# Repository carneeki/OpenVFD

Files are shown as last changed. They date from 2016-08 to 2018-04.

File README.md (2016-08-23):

# OpenVFD
Variable Frequency Drive for ATmega328 based Arduinos

A variable frequency drive is a method for controlling AC motors, typically used
in machinery such as a drill press, milling machine or lathe. A VFD typically
permits the use of running 3 phase motors on single phase power, and running
single phase motors on 3 phase power.

The Arduino code presented here will produce 3 PWM signals that approximate sine
waves suitable to drive some transistors that can be used to power AC motors.

EAGLE schematics will later pop up with potential (but untested) circuits that
can be used connect machinery.

VFDs follow several stages, and can be broken up into 3 separate circuits:

1. AC->DC rectification. This means that AC coming in is turned into DC power.
DC power is smoothed out for fewer ripples. This is where 3 phase really shines, there's a lot less ripple.
1. DC->AC inverter. Gnomes receive signals from a controller to turn a bunch of
switches on and off really fast so the motor thinks it sees AC power. Depending
on how fast the gnomes are clicking the switches controls how fast the motor
spins.
1. The controller is the final circuit, which the Arduino code concerns itself
with.

## AC->DC rectification
For single phase circuits, a standard bridge rectifier can be used.
For three phase circuits, a 3 phase rectifier is required (can be made from 6 diodes).

Once DC comes in, a smoothing capacitor (or a bank of them) is required. The
size of the caps depends on the power in and power out.

## DC->AC inverter
The gnomes mentioned are actually MOSFETs, a type of transistor. 6 of them are
hooked up with 3 in parallel from +DC to one leg of each motor. The other three
are connected from each leg of the motor to GND. The gate (or signal receiver)
needs to be hooked up correctly to the controller.

## Inverter Controller
This circuit consists of an Arduino producing three PWM sine waves that go
through a low pass filter. The low pass filter then goes into a device called a comparator. When the sine wave is high, one pin is turned on and goes to the
MOSFET connected to +DC and motor, the other pin is turned off which goes to
the MOSFET connected to the motor and GND.

Certain MOSFETs have trouble remaining on when high voltages are pushed through
them, so it may be necessary to use a controller chip that prevents certain
dangerous conditions, as well as providing an idea of how much juice the motor
is drawing.

## Thanks and references
Much of this code is very very similar to the works found at CPSU and AMAC
below, but with more comments, and designed for use in driving motors.

Omar David Munoz, senior project,
California Polytechnic State University
http://digitalcommons.calpoly.edu/cgi/viewcontent.cgi?article=1129&context=eesp

Martin Nawrath, "Arduino DDS Sine Wave Generator",
Academy of Media Arts Cologne
http://interface.khm.de/index.php/lab/interfaces-advanced/arduino-dds-sinewave-generator/

And the datasheet which is referenced quite a lot in OpenVFD.ino
http://www.atmel.com/images/Atmel-8271-8-bit-AVR-Microcontroller-ATmega48A-48PA-88A-88PA-168A-168PA-328-328P_datasheet_Complete.pdf

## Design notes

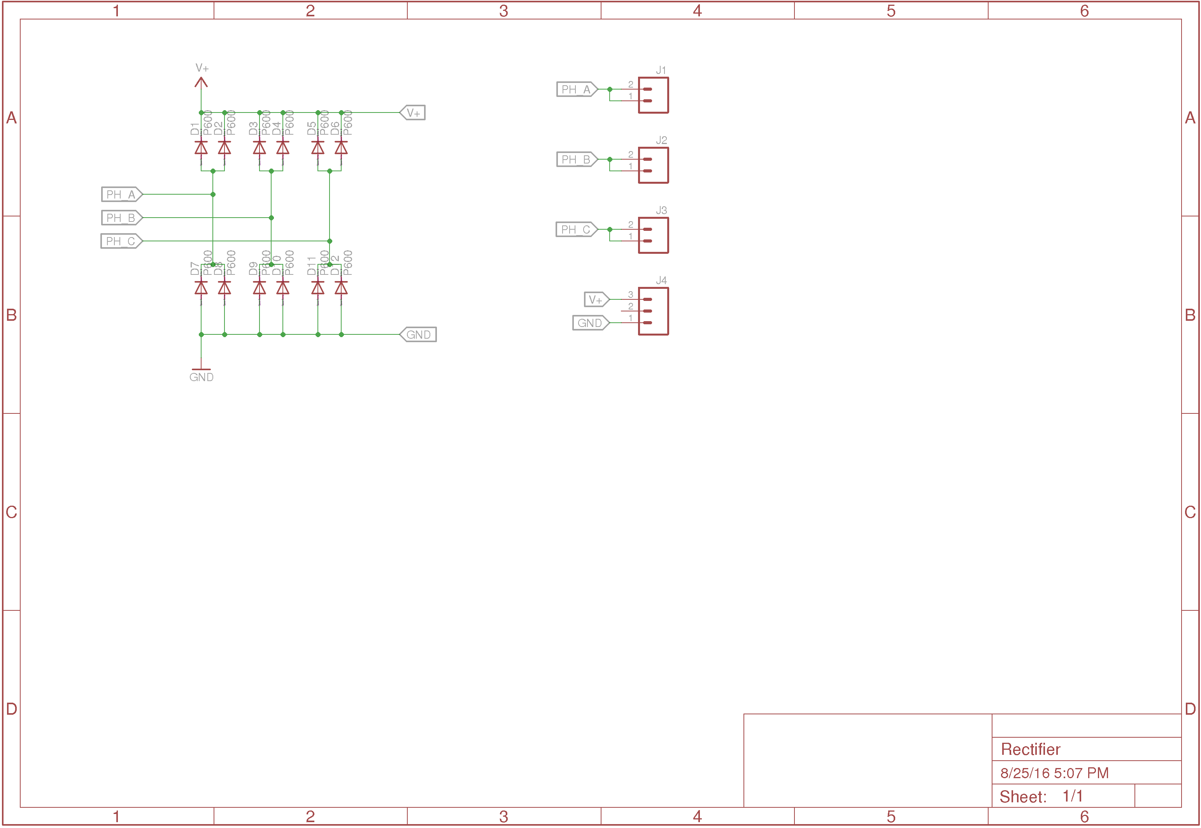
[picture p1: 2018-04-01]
cad/Rectifier Schematic.png

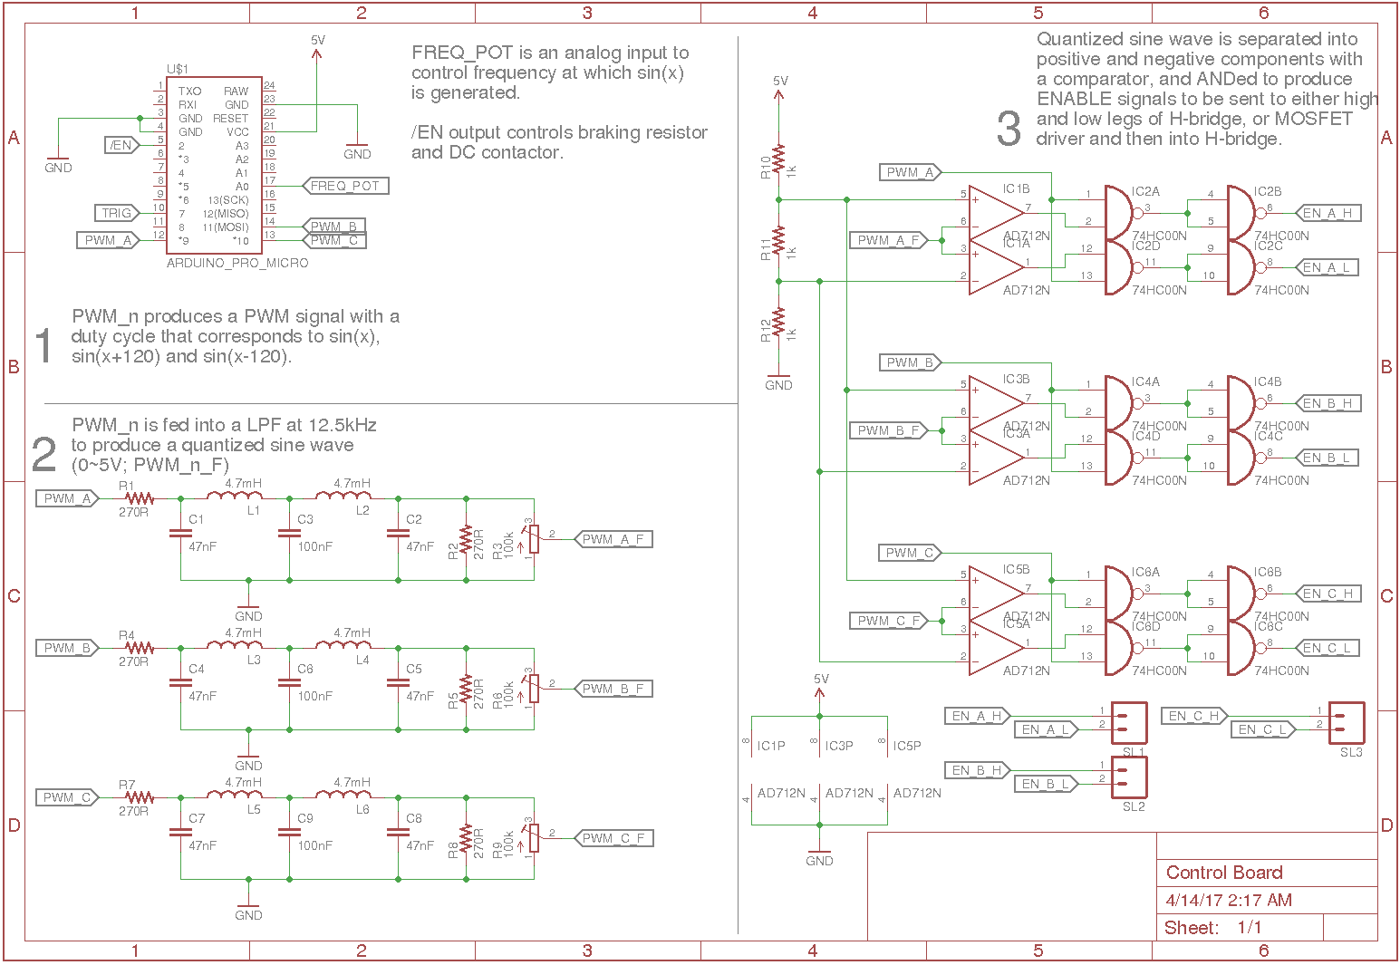
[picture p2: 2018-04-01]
cad/Control Schematic.png

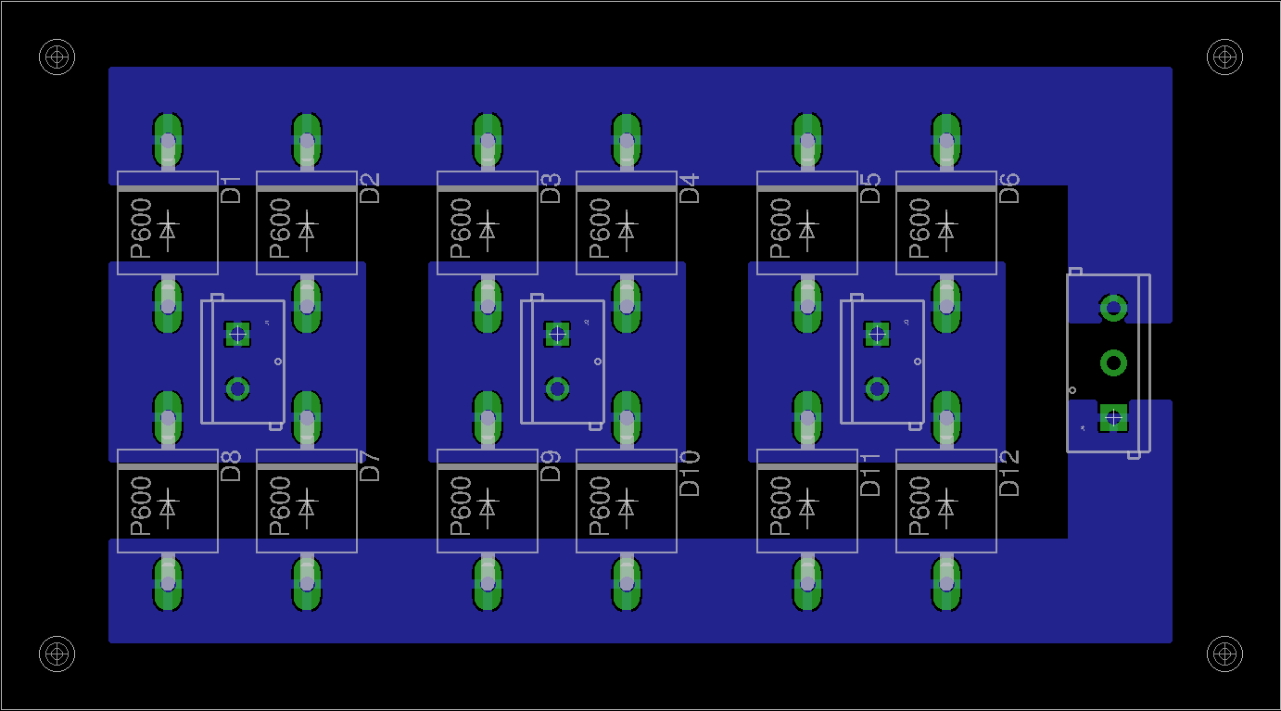
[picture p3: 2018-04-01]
cad/Rectifier Board.png

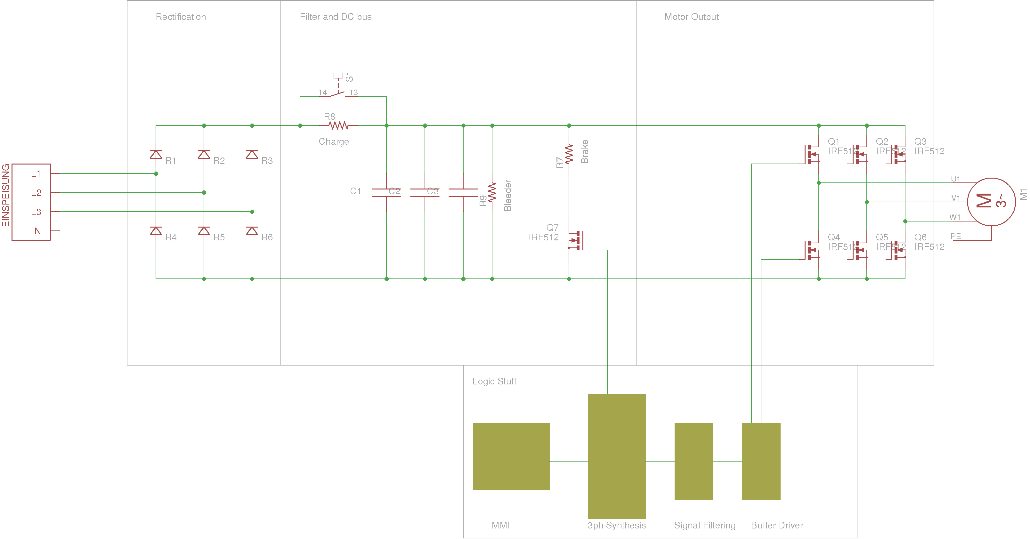
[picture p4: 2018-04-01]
cad/Block Diagram.png

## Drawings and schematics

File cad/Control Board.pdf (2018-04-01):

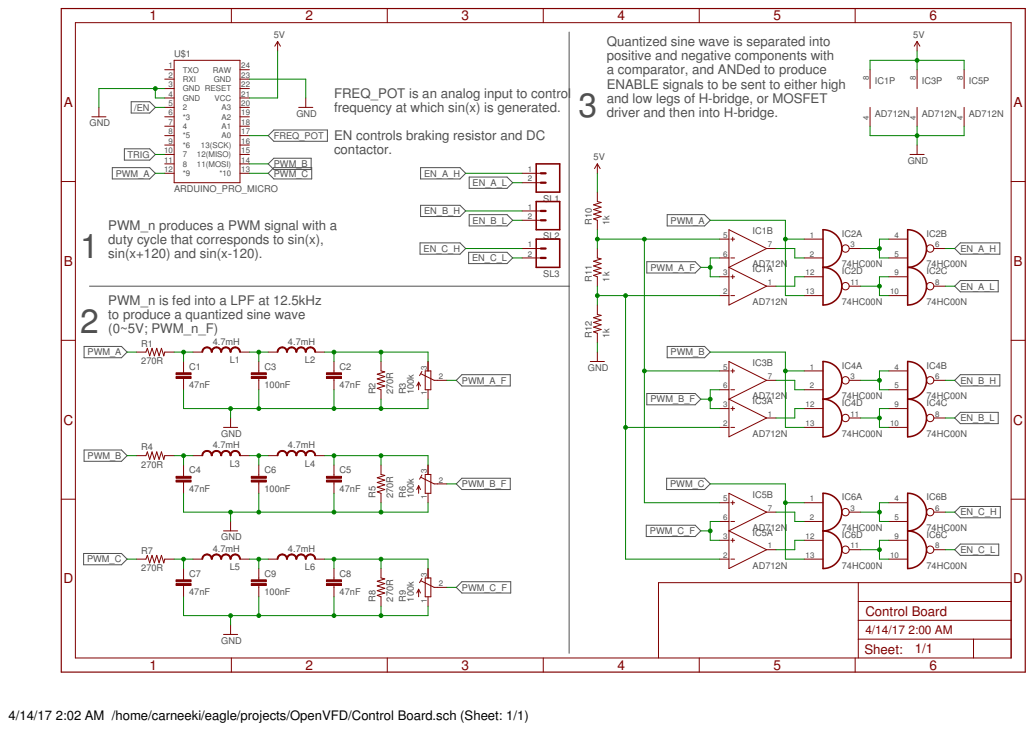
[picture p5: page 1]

Quantized sine wave is separated into
positive and negative components with
a comparator, and ANDed to produce
ENABLE signals to be sent to either high
and low legs of H-bridge, or MOSFET

FREQ_POT is an analog input to control
frequency at which sin(x) is generated. EN controls braking resistor and DC

driver and then into H-bridge. 1
GND

PWM_n produces a PWM signal with a
duty cycle that corresponds to sin(x), sin(x+120) and sin(x-120).
to produce a quantized sine wave
(0~5V; PWM_n_F)

PWM_n is fed into a LPF at 12.5kHz

4/14/17 2:02 AM /home/carneeki/eagle/projects/OpenVFD/Control Board.sch (Sheet: 1/1)

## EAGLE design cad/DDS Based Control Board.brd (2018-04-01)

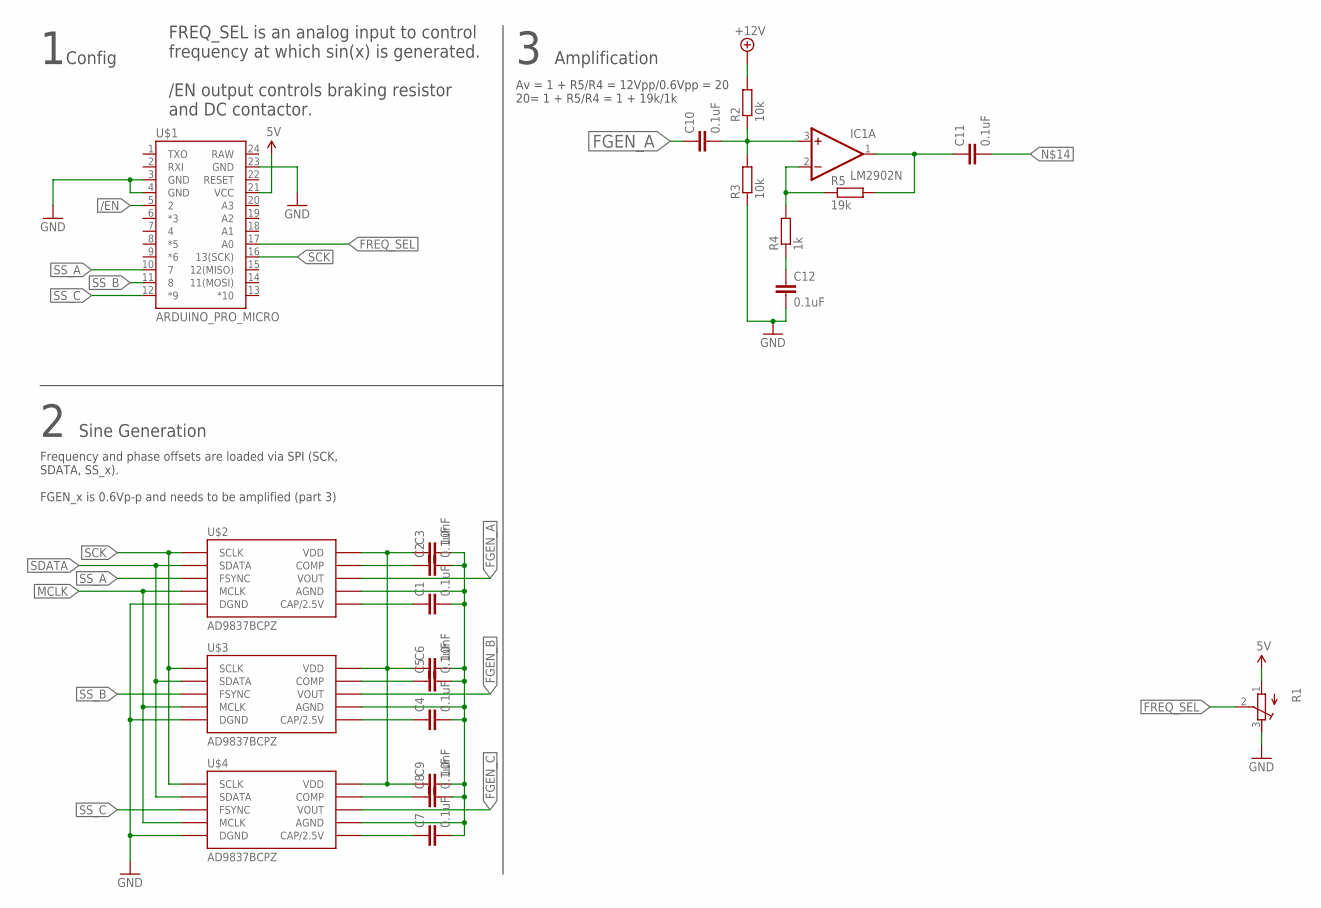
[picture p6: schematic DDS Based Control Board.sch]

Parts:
C1, C2, C4, C5, C7, C8, C10, C11, C12: 0.1uF; C025-025X050
C3, C6, C9: 10nF; C025-025X050
IC1: LM2902N; DIL14
R1: R-TRIMM64X; RTRIM64X
R2, R3: 10k; 0207/7
R4: 1k; 0207/7
R5: 19k; 0207/7
U$1: ARDUINO_PRO_MICRO
U$2, U$3, U$4: AD9837BCPZ; AD9837

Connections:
5V: R1.1 (A)
+12V: R2.2
/EN: U$1.5 (2)
FGEN_A: C10.1, U$2.P$10 (VOUT)
FGEN_B: U$3.P$10 (VOUT)
FGEN_C: U$4.P$10 (VOUT)
FREQ_SEL: R1.2 (S), U$1.17 (A0)
GND: C12.2, R1.3 (E), R3.1, U$1.3 (GND), U$1.4 (GND), U$1.23 (GND)
MCLK: U$2.P$5 (MCLK), U$3.P$5 (MCLK), U$4.P$5 (MCLK)
unnamed: C3.1, C6.1, C9.1, U$2.P$2 (VDD), U$3.P$2 (VDD), U$4.P$2 (VDD)
unnamed: C1.2, C2.2, C3.2, C4.2, C5.2, C6.2, C7.2, C8.2, C9.2, U$2.P$9 (AGND), U$3.P$9 (AGND), U$4.P$9 (AGND)
unnamed: C1.1, U$2.P$3 (CAP/2.5V)
unnamed: U$2.P$0 (DGND), U$2.P$4 (DGND), U$3.P$0 (DGND), U$3.P$4 (DGND), U$4.P$0 (DGND), U$4.P$4 (DGND)
unnamed: C2.1, U$2.P$1 (COMP)
unnamed: C5.1, U$3.P$1 (COMP)
unnamed: C8.1, U$4.P$1 (COMP)
unnamed: C7.1, U$4.P$3 (CAP/2.5V)
unnamed: C4.1, U$3.P$3 (CAP/2.5V)
unnamed: C10.2, IC1.3 (+IN), R2.1, R3.2
unnamed: C11.1, IC1.1 (OUT), R5.2
unnamed: IC1.2 (-IN), R4.2, R5.1
unnamed: C12.1, R4.1
SCK: U$1.16 (13(SCK)), U$2.P$7 (SCLK), U$3.P$7 (SCLK), U$4.P$7 (SCLK)
SDATA: U$2.P$6 (SDATA), U$3.P$6 (SDATA), U$4.P$6 (SDATA)
SS_A: U$1.10 (7), U$2.P$8 (FSYNC)
SS_B: U$1.11 (8), U$3.P$8 (FSYNC)
SS_C: U$1.12 (*9), U$4.P$8 (FSYNC)
V+: IC1.4 (V+)
V-: IC1.11 (V-)
VCC: U$1.21 (VCC)

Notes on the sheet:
FREQ_SEL is an analog input to control frequency at which sin(x) is generated. /EN output controls braking resistor and DC contactor.
Frequency and phase offsets are loaded via SPI (SCK, SDATA, SS_x). FGEN_x is 0.6Vp-p and needs to be amplified (part 3)
Config
Sine Generation
Amplification
Av = 1 + R5/R4 = 12Vpp/0.6Vpp = 20 20= 1 + R5/R4 = 1 + 19k/1k

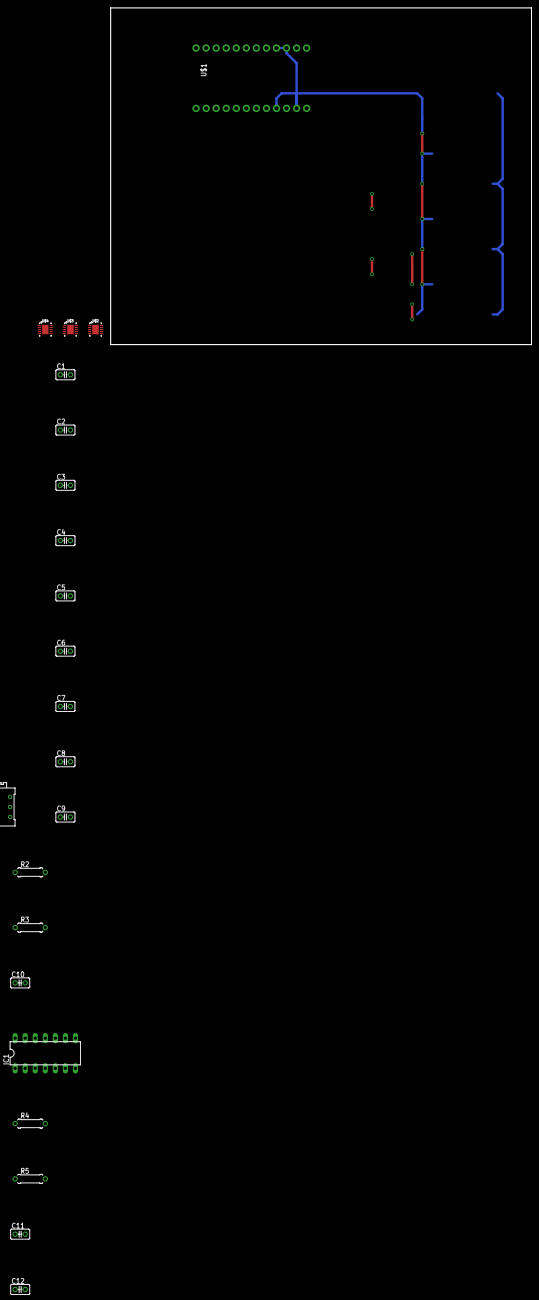
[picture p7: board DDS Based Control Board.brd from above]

Board: 2 copper layers, 106.3 x 85.1 mm, 22 parts (0 on the bottom side), 22 nets.

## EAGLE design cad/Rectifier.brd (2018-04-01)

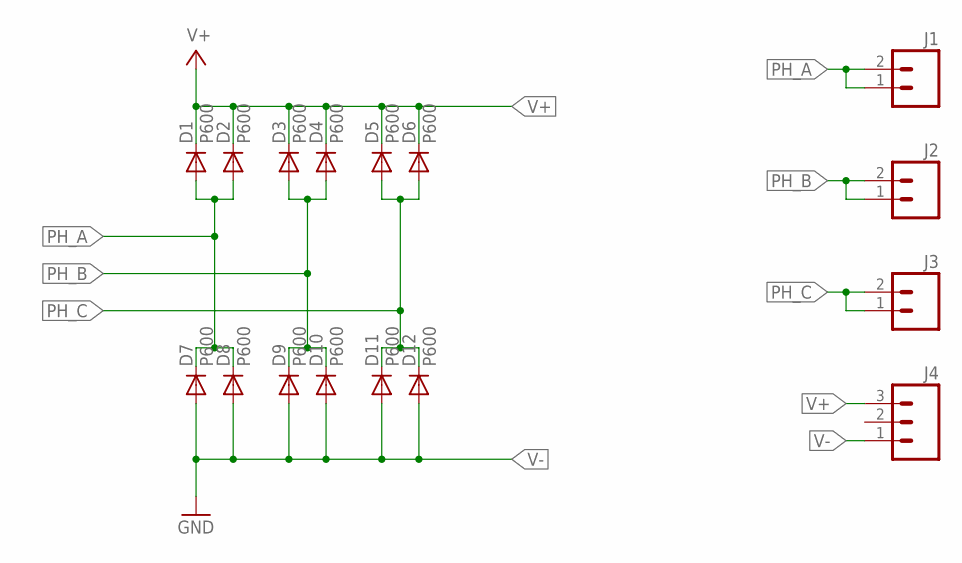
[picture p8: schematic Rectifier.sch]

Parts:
D1, D2, D3, D4, D5, D6, D7, D8, D9, D10, D11, D12: P600; P6-15
J1, J2, J3: M025MM; SCREWTERMINAL-5MM-2
J4: M03-SCREW-5MM; SCREWTERMINAL-5MM-3

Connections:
PH_A: D1.A, D2.A, D7.C, D8.C, J1.1, J1.2
PH_B: D3.A, D4.A, D9.C, D10.C, J2.1, J2.2
PH_C: D5.A, D6.A, D11.C, D12.C, J3.1, J3.2
V+: D1.C, D2.C, D3.C, D4.C, D5.C, D6.C, J4.3
V-: D7.A, D8.A, D9.A, D10.A, D11.A, D12.A, J4.1

Board: 2 copper layers, 16 parts (0 on the bottom side), 5 nets, no tracks yet.

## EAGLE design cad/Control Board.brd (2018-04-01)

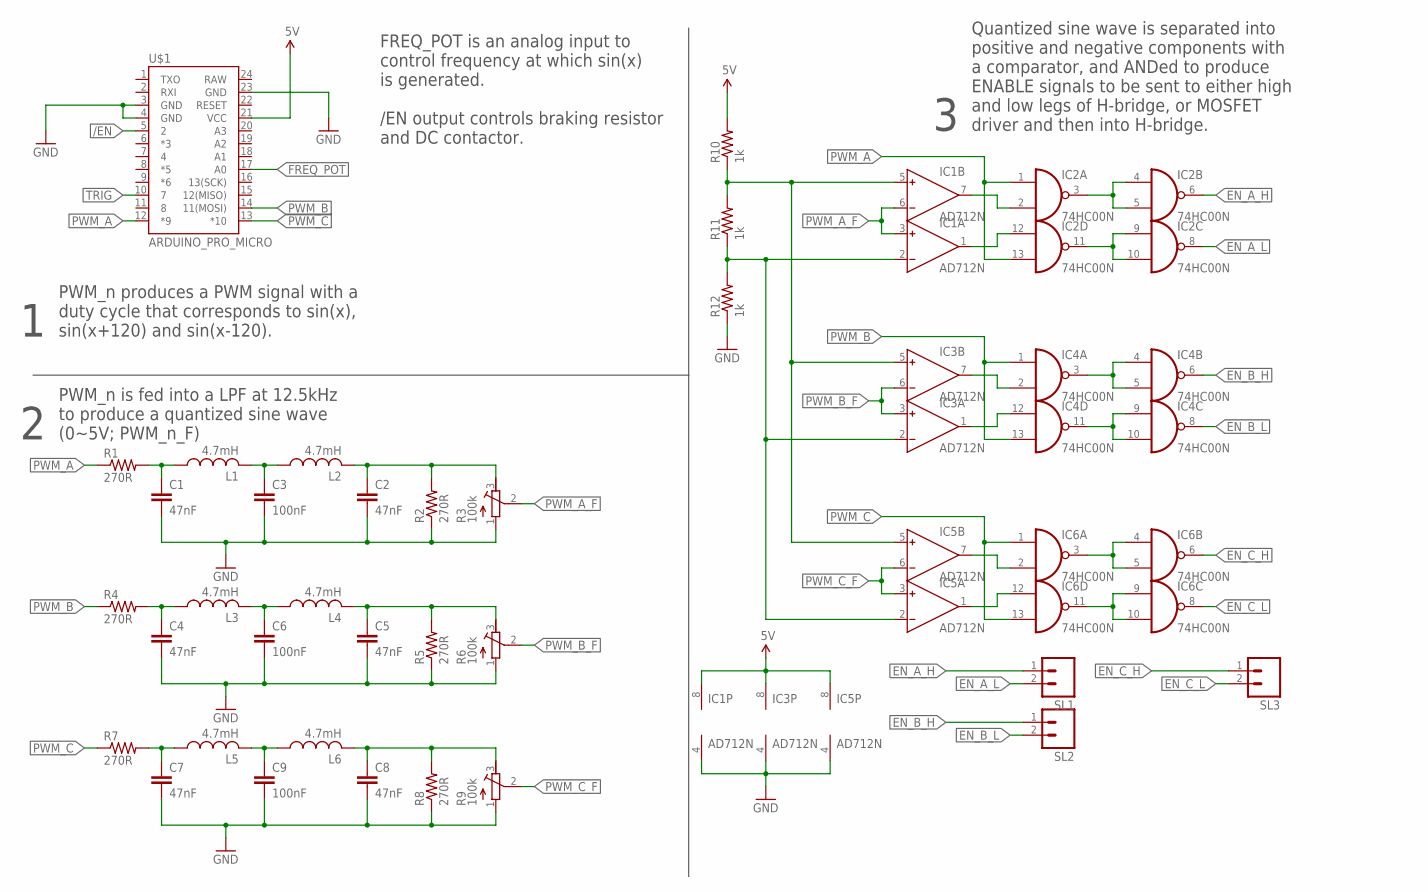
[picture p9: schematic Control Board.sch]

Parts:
C1, C2, C4, C5, C7, C8: 47nF; C025-025X050
C3, C6, C9: 100nF; C025-025X050
IC1, IC3, IC5: AD712N; DIL08
IC2, IC4, IC6: 74HC00N; DIL14
L1, L2, L3, L4, L5, L6: 4.7mH; 0207/12
R1, R2, R4, R5, R7, R8: 270R; 0207/7
R3, R6, R9: 100k; RTRIM3296W
R10, R11, R12: 1k; 0207/7
SL1, SL2, SL3: M02PTH; 1X02
U$1: ARDUINO_PRO_MICRO

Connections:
/EN: U$1.5 (2)
EN_A_H: IC2.6 (O), SL1.1
EN_A_L: IC2.8 (O), SL1.2
EN_B_H: IC4.6 (O), SL2.1
EN_B_L: IC4.8 (O), SL2.2
EN_C_H: IC6.6 (O), SL3.1
EN_C_L: IC6.8 (O), SL3.2
FREQ_POT: U$1.17 (A0)
GND: C1.2, C2.2, C3.2, C4.2, C5.2, C6.2, C7.2, C8.2, C9.2, IC1.4 (V-), IC2.7 (GND), IC3.4 (V-), IC4.7 (GND), IC5.4 (V-), IC6.7 (GND), R2.1, R3.1 (A), R5.1, R6.1 (A), R8.1, R9.1 (A), R12.1, U$1.3 (GND), U$1.4 (GND), U$1.23 (GND)
unnamed: C1.1, L1.1, R1.2
unnamed: C3.1, L1.2, L2.1
unnamed: C2.1, L2.2, R2.2, R3.3 (E)
unnamed: C4.1, L3.1, R4.2
unnamed: C6.1, L3.2, L4.1
unnamed: C5.1, L4.2, R5.2, R6.3 (E)
unnamed: C7.1, L5.1, R7.2
unnamed: C9.1, L5.2, L6.1
unnamed: C8.1, L6.2, R8.2, R9.3 (E)
unnamed: IC1.7 (OUT), IC2.2 (I1)
unnamed: IC1.1 (OUT), IC2.12 (I0)
unnamed: IC3.7 (OUT), IC4.2 (I1)
unnamed: IC1.5 (IN+), IC3.5 (IN+), IC5.5 (IN+), R10.1, R11.2
unnamed: IC1.2 (IN-), IC3.2 (IN-), IC5.2 (IN-), R11.1, R12.2
unnamed: IC3.1 (OUT), IC4.12 (I0)
unnamed: IC5.7 (OUT), IC6.2 (I1)
unnamed: IC5.1 (OUT), IC6.12 (I0)
unnamed: IC2.3 (O), IC2.4 (I0), IC2.5 (I1)
unnamed: IC2.9 (I0), IC2.10 (I1), IC2.11 (O)
unnamed: IC4.3 (O), IC4.4 (I0), IC4.5 (I1)
unnamed: IC4.9 (I0), IC4.10 (I1), IC4.11 (O)
unnamed: IC6.9 (I0), IC6.10 (I1), IC6.11 (O)
unnamed: IC6.3 (O), IC6.4 (I0), IC6.5 (I1)
PWM_A: IC2.1 (I0), IC2.13 (I1), R1.1, U$1.12 (*9)
PWM_A_F: IC1.3 (IN+), IC1.6 (IN-), R3.2 (S)
PWM_B: IC4.1 (I0), IC4.13 (I1), R4.1, U$1.14 (11(MOSI))
PWM_B_F: IC3.3 (IN+), IC3.6 (IN-), R6.2 (S)
PWM_C: IC6.1 (I0), IC6.13 (I1), R7.1, U$1.13 (*10)
PWM_C_F: IC5.3 (IN+), IC5.6 (IN-), R9.2 (S)
TRIG: U$1.10 (7)
VCC: IC1.8 (V+), IC2.14 (VCC), IC3.8 (V+), IC4.14 (VCC), IC5.8 (V+), IC6.14 (VCC), R10.2, U$1.21 (VCC)

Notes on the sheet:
FREQ_POT is an analog input to control frequency at which sin(x) is generated. /EN output controls braking resistor and DC contactor.
PWM_n is fed into a LPF at 12.5kHz to produce a quantized sine wave (0~5V; PWM_n_F)
Quantized sine wave is separated into positive and negative components with a comparator, and ANDed to produce ENABLE signals to be sent to either high and low legs of H-bridge, or MOSFET driver and then into H-bridge.
PWM_n produces a PWM signal with a duty cycle that corresponds to sin(x), sin(x+120) and sin(x-120).

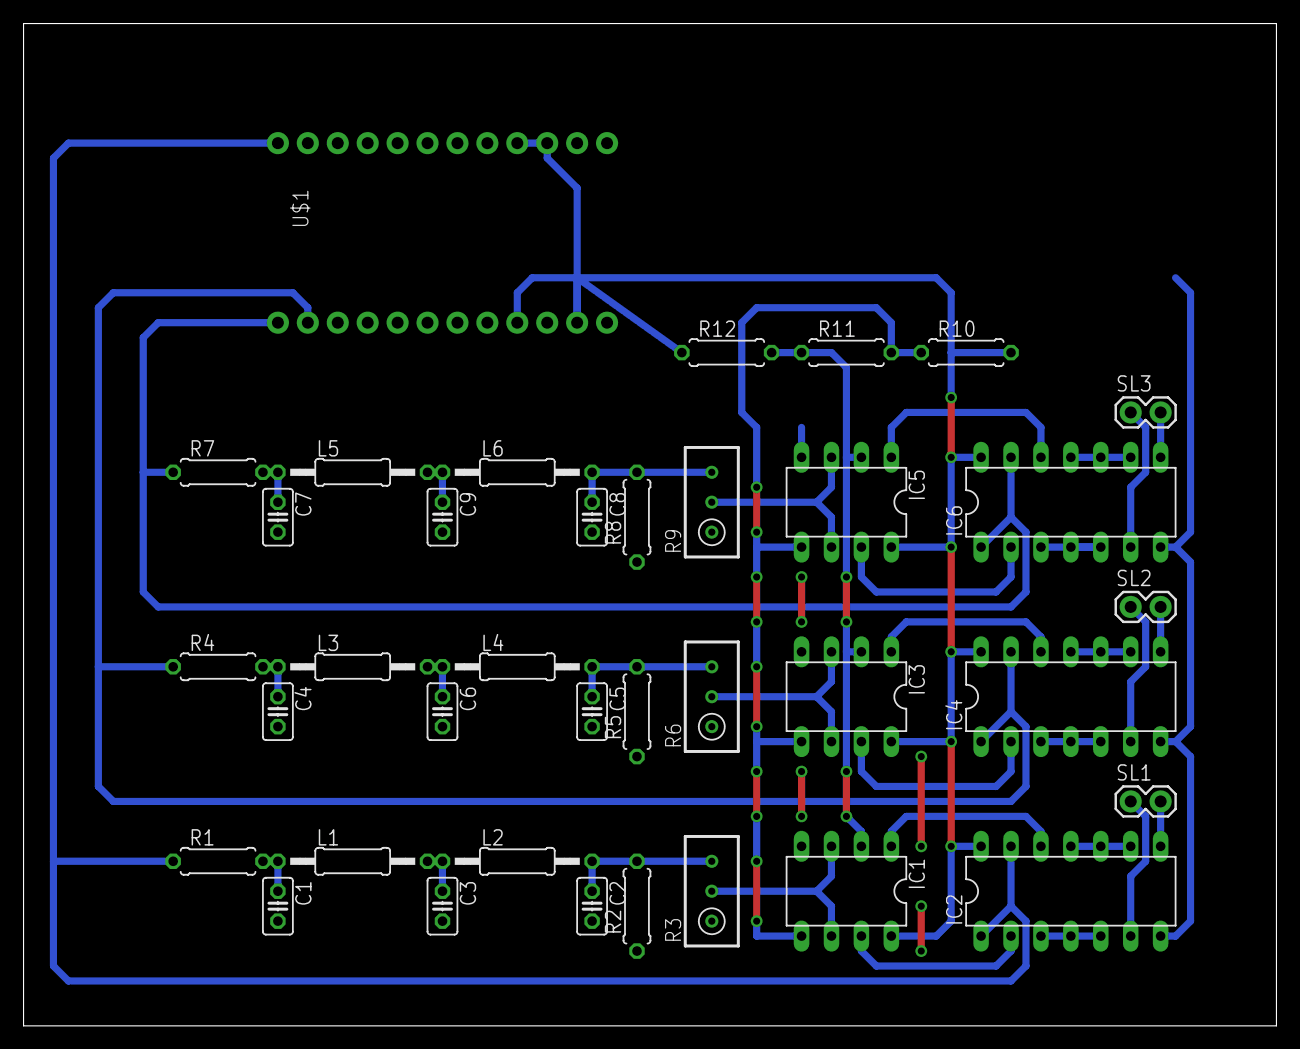
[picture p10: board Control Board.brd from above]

Board: 2 copper layers, 106.3 x 85.1 mm, 37 parts (0 on the bottom side), 37 nets.

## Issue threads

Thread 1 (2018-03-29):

can you share a working circuit for VFD along with arduino?

amrithmmh, 2018-03-29:
i am really interested in your project thanks

carneeki, 2018-04-01:
This project had to take a bit of a back seat for a while, but I want to get back on it soon!

I've just pushed some cad files I was working on a while ago, I'm not sure if they will work, but feel free to review them. If nothing else, the block diagram might be a good place to start a new VFD project.

amrithmmh, 2018-04-25:
you might be interested in this
http://www.microchip.com//wwwAppNotes/AppNotes.aspx?appnote=en567897
http://ww1.microchip.com/downloads/en/AppNotes/00001660B.pdf
file:///C:/Users/Novatek/AppData/Local/Temp/BNZ.5ae0150e714456/219-0503c_SCH.pdf

carneeki, 2018-04-25:
These application notes are great thanks! It makes me the idea in my head might be on the right track.

As for knowledge or experience, that hasn't stopped me in the past! My strategy is to set myself some projects and work out what I need to learn, and then learn it. With mixed results ;)

carneeki, 2018-04-25:
As I don't know what your experience is... I should mention a word of caution though: VFDs typically operate at voltages that can be lethal. If you're new to electronics, I would recommend starting off with some low voltage projects (anything between 0 and 12V should be fine) to build up your skills, and use bought power supplies that have passed the important safety checks.

amrithmmh, 2018-04-25:
there are many ICs from microchip too that have application notes you can check out those too
and one more IC
https://www.nxp.com/docs/en/data-sheet/MC3PHAC.pdf
http://application-notes.digchip.com/314/314-67275.pdf
http://sroogle.ru/?q=MC3PHAC
http://www.electronics-lab.com/project/3-phase-ac-motor-controller/
MC3PHAC is retired though :(

carneeki, 2018-04-25:
True, I've got a couple of PIC chips in a drawer somewhere, however, I'm thinking something like the Arduino Nano will have less of a steep learning curve to people like CNC machinists who may be wanting to build a VFD. Plug USB cable in and push the 'Upload' button.

If something like a USBasp or PICkit are needed for ICSP, that adds an additional barrier to entry. If I were making a commercial product, I'd look at going either PIC or AVR without the Arduino framework, but keeping it accessible for the mechatronics enthusiast is important.

dexterbot80, 2019-02-07:
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
Hello, Here is an update for testing PCB . I hope it will work :)

dexterbot80, 2019-02-07:
What are the TRIG and / EN pins? Thank you

carneeki, 2019-02-08:
Hi @dexterbot80  the board looks great!

TRIG is to trigger an oscilloscope (during testing / calibration) - see line `19` in `OpenVFD.ino` ;)
/EN I think was to be an "Enable" pin where pulling it low would enable the PWM outputs and pulling it high would disable the outputs, this is because controllers like Grbl often use a "Spindle Enable" output pin to tell the VFD to start the spindle, but it could also be used for a manual switch. A simple `if()` inside of `loop()` should be all that's needed to make it functional.

dexterbot80, 2019-02-08:
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
Thank you

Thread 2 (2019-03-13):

Inappropriate transistors

Harvie, 2019-03-13:
Hi! according to Block Diagram.png you are using IRF512 transistors, but i've checked datasheet and these came in 100V maximum rating. I guess that commercial VFDs use IGBT transistors... Don't know.

But you surely get more  than 100V when rectifiing mains AC, no matter if US 120V or EU 230V...
Also 230V is RMS, while after rectification you get peak value 320V rather than the RMS. (multiply by factor of 1.41421)
But if you are rectifiing 3 phases, that's different story. There is 400V RMS between two phases, which means peak is something like 566V, so that's what you get after rectifiing 3F mains in EU. (multiply by 1.5708)

So to know what voltage you THEORETICALY get after rectification of 3 phases:

**EU: 230*1.5708*1.41421 = 511V
US: 120*1.5708*1.41421 = 267V**

Note that the voltage in grid fluctuates a little. Also you should leave some safety margin.

Please keep that in mind.

carneeki, 2019-03-14:
@Harvie absolutely correct on the count of voltage, nice find. :)

IIRC, the block diagram was the very first diagram I did to get a "big picture" overview - the idea being that each area of the diagram would have separate schematics with values, and I likely forgot to remove the component values from the block diagram.

I seem to remember another IRF branded IGBT in the output schematic with a voltage rating of 600V, and thinking that 90V for AU (also 230V, +8%/-10%) wasn't a lot of margin [in theory could be about 680V for our power here]... However, there are two IGBTs in series (as well as the motor) along each path from +ve to GND along the DC bus, so it works out to about 300V across the drain and source on each IGBT.

Out of curiosity, where does 1.5708 come from? I recognise 1.414... = sqrt(2), and 1.732... = sqrt(3) which were both common constants in 3ph power calculations, but 1.5708... is a new one to me.

Thanks again for spotting this :)

Harvie, 2019-03-14:
> Out of curiosity, where does 1.5708 come from?

I am not really sure, since i've never designed 3 phase appliance. I've just googled the number and 1.57 seems to repeat through te internet. However i draw these two green arrows to the following diagram. I seems to be more like 1.5 or 1.49 in picture, i don't know why everybody uses 1.57. Maybe i am missing something. But i guess there's more to it:

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

> However, there are two IGBTs in series (as well as the motor) along each path from +ve to GND along the DC bus

I don't think so:

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

If you want possitive voltage on U1, you have to open Q1 and close Q4. That would mean that Q4 gets full DC rail voltage.

Also you can't assume anything about the motor. VFDs should be able to work with low-impedance low-voltage motors for several reasons.

1.) when you lower the RPM, you lower the frequency and the impedance goes very low. That's why common VFDs for CNC spindles have to dramaticaly lower the sine voltage at the low RPMs. That's why all VFDs have programmable voltage/frequency curves.

2.) you might want VFD to drive small motor that can't handle 230V at all. For example you might want to drive small BLDC motor using VFD.

3.) VFD should have closed-loop current sensing. I've accidentaly managed to get some metalic chips to the connector of my CNC spindle and that effectively created short circuit of VFD. I should have been more carefull, but to be honest the metalic shavings are very common around CNC.
I am very happy that VFD managed to detect the short circuit, stop itself and display appropriate error message instead of exploding transistors...

carneeki, 2019-03-14:
> But i guess there's more to it:
Perhaps this image will help?
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

It's from the section of [Full-wave Three-phase Rectifier Conduction Waveform](https://www.electronics-tutorials.ws/power/three-phase-rectification.html) here which offers an explanation of a slightly higher than 1.57x constant (approx 1.65) is needed. Overlayed with a variation on your image I think it makes sense:
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

I took your P2 to P1 voltage and copy+pasted it next to the yellow line I drew and the yellow line is longer just a little bit either side of the valley - the gradient of P3 is near zero so the rate of change is also near zero, but the gradient of P2 is closer to 1 so the rate of change is more. (btw, I honestly never thought I'd use calculus in a discussion on the internet :D !)

> If you want possitive voltage on U1, you have to open Q1 and close Q4. That would mean that Q4 gets full DC rail voltage.
Yep - this is true... It makes more sense now that I see the H-bridge on paper again, and to pretend the IGBTs are switches.

Concerning:
1. Lower voltage - I think they simply use PWM to do this in software no? Would be interesting to put an oscilloscope on the output terminals of the FETs to take a look. If so, this become a matter of software chopping the open/close ratios.
2. Low voltage DC would also be a matter of software chopping PWM, but maybe with additional timing constraints - I've never looked at BLDC control before.
3. The output schematic includes an IRS2336, the [datasheet](https://www.infineon.com/dgdl/Infineon-IRS2336-DS-v02_00-EN.pdf?fileId=5546d462533600a40153567ab2a0280e) indicates it has short and shoot-thru protections, as well as fault reporting. It requires hooking up the Itrip pin to some shunt resistors. I'll add that to the growing TODO list :)

Harvie, 2019-03-14:
> I think they simply use PWM to do this in software no?

Of course. But that was not my point. My point is that in such case you have to drop all DC rail voltage on the transistor, so you can't count with motor to drop any aditional voltage to save your transistors.

> Low voltage DC would also be a matter of software chopping PWM.  I've never looked at BLDC control before.

BLDC is exactly the same as 3 phase AC motor. The **DC** in BLDC stands just for the fact that they use "speed controller" to run on DC. Speed controller is basicaly just VFD without rectifier on input. BLDC terminology is used by RC model people (drones, rc airplanes, e-bikes, etc...), so that means BLDC motor usualy runs much lower voltages, because they use batteries to power them. Technicaly speaking it's exactly the same as AC motor. The BLDC term is bit misleading... But if you think about it... Even brushed DC motors run on AC. They just have to create it using brushes.

> The output schematic includes an IRS2336, the datasheet indicates it has short and shoot-thru protections, as well as fault reporting.

This is very cool! At least if that's really true... Is it really protecting short through the IGBTs? Or it's just protecting the driver output from being shorted?

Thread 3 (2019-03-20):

Your proposed circuit is wrong,

dexterbot80, 2019-03-20:
The AD712 comparator requires differential input voltage. https://www.analog.com/media/en/technical-documentation/data-sheets/ad712.pdf
I replaced with LM358N but the IGBT bridge goes into short circuit immediately after the start.
http://www.ti.com/lit/ds/symlink/lm158-n.pdf

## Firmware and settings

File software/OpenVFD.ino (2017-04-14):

#include "avr/pgmspace.h" // PROGMEM and pgm_read_byte_near()
#include "avr/io.h"

/* Reference clock needs to be measured for the crystal per board (about 16MHz).
 * It is then divided by 510.
 * 16M / 510 = 31372.5490
 */
#define REFCLK 31372.549 // TODO: measure me and adjust

// output frequency
#define FREQ_POT A0  // analog input (A0..A4 are valid) default: A0
#define FREQ_MIN 0   // default: 0
#define FREQ_MAX 100 // default: 100

// pot values might not permit cranking full range so adjust here
#define POT_MIN 0    // default: 0
#define POT_MAX 1023 // default: 1023

// pins for 3 phases: Alpha, Bravo, Charlie, and trigger for CRO.
// ATMega 168 / 328 valid PWM pins are 3,5,6,9,10,11. Non-default values have
// not been tested
#define PWM_A  9     // default:  9
#define PWM_B 10     // default: 10
#define PWM_C 11     // default: 11
#define TRIG   7     // default:  7

/*******************************************************************************
 * Should not need to configure anything below here ***************************/

/*
 * LUT for sin(t) generated (by spreadsheet) using this formula:
 * x = ROUND( (255/2) * (1+SIN((2*PI()) * (t/256))) )
 *
 * where 0 <= t <= 255 ; keeping one period of sine in nvram
 *
 * Keeping LUT is way faster than calculating all the time
 */
const byte sin256[] PROGMEM =
{
//  0   1   2   3   4   5   6   7   8   9   a   b   c   d   e   f
  128,131,134,137,140,143,146,149,152,155,158,162,165,167,170,173, // 00:0f
  176,179,182,185,188,190,193,196,198,201,203,206,208,211,213,215, // 10:1f
  218,220,222,224,226,228,230,232,234,235,237,238,240,241,243,244, // 20:2f
  245,246,248,249,250,250,251,252,253,253,254,254,254,255,255,255, // 30:3f
  255,255,255,255,254,254,254,253,253,252,251,250,250,249,248,246, // 40:4f
  245,244,243,241,240,238,237,235,234,232,230,228,226,224,222,220, // 50:5f
  218,215,213,211,208,206,203,201,198,196,193,190,188,185,182,179, // 60:6f
  176,173,170,167,165,162,158,155,152,149,146,143,140,137,134,131, // 70:7f
  128,124,121,118,115,112,109,106,103,100, 97, 93, 90, 88, 85, 82, // 80:8f
   79, 76, 73, 70, 67, 65, 62, 59, 57, 54, 52, 49, 47, 44, 42, 40, // 90:9f
   37, 35, 33, 31, 29, 27, 25, 23, 21, 20, 18, 17, 15, 14, 12, 11, // a0:af
   10,  9,  7,  6,  5,  5,  4,  3,  2,  2,  1,  1,  1,  0,  0,  0, // b0:bf
    0,  0,  0,  0,  1,  1,  1,  2,  2,  3,  4,  5,  5,  6,  7,  9, // c0:cf
   10, 11, 12, 14, 15, 17, 18, 20, 21, 23, 25, 27, 29, 31, 33, 35, // d0:df
   37, 40, 42, 44, 47, 49, 52, 54, 57, 59, 62, 65, 67, 70, 73, 76, // e0:ef
   79, 82, 85, 88, 90, 93, 97,100,103,106,109,112,115,118,121,124  // f0:ff
};

// phase offsets (n * 255 / 3)
#define A_OFFSET 0   // (0x00)
#define B_OFFSET 85  // (0x55)
#define C_OFFSET 170 // (0xaa)

int freq; // output frequency
const double TUN_K=( 4294967296.0 / REFCLK ); // tuning coefficient

// variables in ISR
volatile byte icnt;            //
volatile byte icnt1;           //
volatile byte c4ms;            // counter incremented every 4ms
volatile unsigned long phaccu; // phase accumulator
volatile unsigned long tune;   // dds tuning word

void setup()
{
  pinMode(PWM_A, OUTPUT);
  pinMode(PWM_B, OUTPUT);
  pinMode(PWM_C, OUTPUT);
  pinMode(TRIG, OUTPUT);

  setup_timers(); // this also disables interrupts
}

void loop()
{
  if(c4ms > 250)
  {
    c4ms = 0;
    freq = map(analogRead(FREQ_POT), POT_MIN, POT_MAX, FREQ_MIN, FREQ_MAX);

    TIMSK2 &= ~(_BV(TOIE2)); // disable Timer2 interrupt
    tune = TUN_K*freq;       // update DDS tuning word
    TIMSK2 |= _BV(TOIE2);    // re-enable Timer2 interrupt
  }
}


/**
 * Set prescaler to 1, PWM mode to phase correct PWM
 * @see https://www.arduino.cc/en/Tutorial/SecretsOfArduinoPWM
 * @see http://www.atmel.com/images/Atmel-8271-8-bit-AVR-Microcontroller-ATmega48A-48PA-88A-88PA-168A-168PA-328-328P_datasheet_Complete.pdf
 * @see datasheet section 15.7.4 "Phase Correct PWM Mode"
 */
void setup_timers()
{
  /* Timer Registers:
   * n = timer n (0,1,2)
   * x = bit X
   * each timer has slightly different config bits, datasheet section 9, 15, 18
   *
   * TCCRnA = Timer/Counter Control Register A
   * TCCRnB = Timer/Counter Control Register B
   * TCCRxx holds the main control bits for the timer
   *
   * CS = Clock Select bits for prescaler (datasheet 9.12.2)
   *
   * COMnA = Comparator Output A
   * COMnB = Comparator Output B
   * Comparator sets levels at which outputs A and B are affected
   */

   /* Disable Timer 0 so it cannot interrupt the loop
    * See Section 15.9.6 */
   TIMSK0 &= ~(_BV(TOIE0));

   /* Enable Timer 1
    * See Section 16.11.8 */
   TIMSK1 |= _BV(TOIE1);

   /* Enable Timer 2
    * See Section 18.11.6 */
   TIMSK2 |= _BV(TOIE2);

  /*** Timer 1 ***/
  /* Timer 1 Clock Prescaler to no prescaling (CS12:0 = 001)
   * Section 16.11.2 Table 16-5 */
  TCCR1B &= ~(_BV(CS12));
  TCCR1B &= ~(_BV(CS11));
  TCCR1B |= _BV(CS10);

  /* Timer 1 Set WGM to Phase Correct PWM 8 bit (WGM13:0 = 0001)
   * Section 16.11.1, Table 16-4 */
  TCCR1B &= ~(_BV(WGM13));
  TCCR1B &= ~(_BV(WGM12));
  TCCR1B &= ~(_BV(WGM11));
  TCCR1B |= _BV(WGM10);

  /* Timer 1 Set Compare Output Mode (COM1A1:0 = COM1B1:0 = 01)
   * Section 16.11.1, Table 16-2 */
  TCCR1A |= _BV(COM1A1);    // Clear OC1A on compare match -- and --
  TCCR1A &= ~(_BV(COM1A0)); // Set OC1A at bottom
  TCCR1A |= _BV(COM1B1);    // Clear OC1B on compare match -- and --
  TCCR1A &= ~(_BV(COM1A0)); // Set OC1B at bottom

  /*** Timer 2 ***/
  /* Timer 2 Clock Prescaler to no prescaling (CS22:0 = 001)
   * Section 18.11.2 */
  TCCR2B &= ~(_BV(CS22));
  TCCR2B &= ~(_BV(CS21));
  TCCR2B |= _BV(CS20);

  /* Timer2 Set WGM to Phase Correct PWM (WGM22:0 = 001)
   * Section 18.7.4 */
  TCCR2B &= ~(_BV(WGM22));
  TCCR2B &= ~(_BV(WGM22));
  TCCR2A |= _BV(WGM20);

  /* Timer 2 Set compare output mode (COM2A1:0 = 01)
   * Section 18.11.1 */
  TCCR2A |= _BV(COM2A1);    // Clear OC2A on Compare Match when up count -- and
  TCCR2A &= ~(_BV(COM2A0)); // Set OC2A on Compare Match when down count.

  // Timer 2 NOTE: we can leave FOC2B:A unset also, bits 4 and 5 are reserved
}


/**
 * Timer 2 interrupt - 31.25kHz ~= 32us
 * Fout = (tuning word * REFCLK) / 2^32
 * Runtime: 8us (incl stack push + pop)
 */
ISR(TIMER2_OVF_vect)
{
  PORTD |= _BV(TRIG);  // Trigger CRO
  phaccu += tune;      // soft DDS, phase accu with 32 bits
  icnt = phaccu >> 24; // use upper 8 bits for phase accu as frequency information

  // read byte from sin256 table using the phase offset as the address
  // place into output compar registers
  OCR2A = pgm_read_byte_near(sin256 + (uint8_t)(icnt + A_OFFSET));
  OCR1A = pgm_read_byte_near(sin256 + (uint8_t)(icnt + B_OFFSET));
  OCR1B = pgm_read_byte_near(sin256 + (uint8_t)(icnt + C_OFFSET));

  if (icnt1++ == 125) // increment variable c4ms every 4 milliseconds
  {
    c4ms++;
    icnt1 = 0;
  }
  PORTD &= ~(_BV(TRIG)); // Reset CRO trigger
}

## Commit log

2017-04-14 fixed OBO problem that caused compiler warnings (and incorrect data) also tidied the LUT and corrected the formula for spreadsheet generation
    [OpenVFD.ino]
2018-04-01 add cad files, move arduino source to folder. this cad has not been looked at in over a year and a bit, it may not work. it may set things on fire. do not use!
    [Block Diagram.sch, Control Board.brd, Control Board.sch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]

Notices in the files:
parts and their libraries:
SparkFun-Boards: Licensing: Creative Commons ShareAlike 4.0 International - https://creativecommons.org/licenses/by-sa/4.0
